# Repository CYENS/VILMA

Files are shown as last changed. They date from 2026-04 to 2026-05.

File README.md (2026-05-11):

# VILMA

This repository contains the codebase for the VILMA (VIsion Language MAnipulation) project, created by the CAIR (Cognitive Artificial Intelligence and Robotics) research group at the CYENS Centre of Excellence. This work was supported by the euROBIN project under the 3rd Open Call for Technology Exchange Programme (Project: "VILMA - Advancing Robotic Manipulation: A Handheld Gripper and Vision-Language Dataset"). 

The repository provides the hardware documentation and software framework for multimodal manipulation data collection using a head-mounted camera, a microphone, and two handheld grippers equipped with cameras and motion tracking systems. It includes tools for sensor synchronization, data acquisition, processing pipelines, and dataset generation.

The VILMA Dataset can be downloaded from our EuroCore Zenodo repository here: https://doi.org/10.5281/zenodo.19708163

## 1. Hardware

Full hardware documentation is available in the `hardware/` folder, that includes:

- Hardware guide
- Full CAD models (STEP, STL, and editable source references)
- Bill of Materials (BOM)
- 3D printing guidelines 
- Assembly instructions with deployment setup guidance
- Interchangeable hard and soft finger configurations
- Integrated HTC VIVE tracker mounting for motion tracking
- GoPro mounting support for egocentric recording
- AprilTags

The design preserves the original UMI pistol-style interaction while introducing project-specific modifications for improved tracking integration, deployment readiness, and real-world data collection reliability.

## 2. Software setup

### 2.1. Clone the repository

```bash
git clone https://github.com/ctheoc/VILMA.git
cd VILMA
```

### 2.2. Create a virtual environment

```bash
python -m venv venv
```

### 2.3. Activate the virtual environment

**Linux / macOS**

```bash
source venv/bin/activate
```

**Windows**

```bash
venv\Scripts\activate
```

### 2.4. Install dependencies

#### 2.4.1 ffmpeg

To check if it's installed, run: 
```bash
which ffprobe
ffprobe -version 
```

If not installed, download from https://ffmpeg.org, or run

**Ubuntu/Debian**
```bash
sudo apt updatesudo apt install ffmpeg 
```

**macOS (Homebrew)**: 
```bash
brew install ffmpeg 
```

#### 2.4.2 Python libraries

```bash
pip install -r requirements.txt
```

## 3. Data Collection

Data are collected using VIVE trackers, GoPro cameras, and microphone.

### 3.1. Finger distance calibration

To account for the severe distortion of the GoPro Hero 13 Black’s 'Ultra Wide HyperView' lens, perform a custom finger distance calibration. Map physical measurements to the pixel distances between the centers of the AprilTags on each finger. 

```bash
python data_collection/vilma_fingers_distance_calibration.py
```

### 3.2. Data Collection setup

#### 3.2.1 Tracking
VIVE trackers and base stations should be connected via SteamVR.
Prerequisites: Download and install SteamVR.
Connect base stations and trackers:
1. Connect the base stations to power.
2. Connect the trackers to the PC:
   - Connect one end of the USB Type-C cable to the dongle cradle, and then plug the dongle into the cradle.
   - Connect the other end of the USB Type-C cable to a USB port on your computer.
   - Note: Keep the dongle at least 45 cm away from the computer and place it where it won’t be moved.
   - From your computer, open the SteamVR app.
   - Click **Menu > Devices > Pair Controller**.
   - Press the Power button for around 2 seconds. The status light will blink blue.
   - Wait for the status light to turn green. This means pairing is successful.
   - In the Controller Pairing window, click **Done**.

#### 3.2.2 Video recording
We use two GoPro HERO13 cameras, each one mounted on each handheld gripper, and a head-mounted GoPro HERO9 camera. HERO13 cameras can be manipulated via this script, while HERO9 is manipulated manually, or via a mobile phone.
Prerequisites: Download GoPro Quik app on the mobile phone.
Setup and connect cameras:
1. Camera settings:
   - GoPro HERO13: 16:9 | 4K | 60 | UHV
   - GoPro HERO9: 4K | 60 | L
2. Connect GoPro HERO13 to the PC:
   - Turn on the cameras and reset wireless connections: **Preferences > Wireless Connections > Reset Connections > Reset All**.
   - Turn on the PC's Bluetooth and Wi-Fi, and delete GoPro cameras from the computers previous connected Bluetooth devices, if any.
   - Select **Pair Device** on cameras.
      
3. Connect GoPro HERO9 to a mobile phone:
   - Turn on the phone's Bluetooth and Wi-Fi, open GoPro Quik, and select GoPro tab.
   - Turn on the camera and select **Connections > Connect Device > Quick App** to connect.

#### 3.2.3 Audio recording
Set up RODE microphone:
1. Connect RX (Receiver) to the PC via USB.
2. Connect TX (Transmitter) to the RX.
3. Select **Wireless GO GX** as the input device in the PC settings.

#### 3.2.4 Check PC audio
Ensure the PC volume is **not muted** so you can hear the 'beep' sound when a recording starts. This sound will be later used to synchronize tracking and video recordings.

### 3.3. Run the data collection script

```bash
python data_collection/vilma_collect_data.py
```

This script creates in the repository root: 
 - a folder with the recorded data named **recordings**, and 
 - a JSON file named **sessions.json** that includes the paths to the data files.

For tracking we use 
https://github.com/TriadSemi/triad_openvr 
at commit d389aacf2a4caa392398613a9daddba15ee24f92.

## 4. Data Processing

### 4.1. Data Processing setup

Make sure that videos exists in the **recordings** folder.
 - Videos captured by the camera mounted on the left gripper under **recordings/left**
 - Videos captured by the camera mounted on the right gripper under **recordings/right**
 - Videos captured by the head-mounted camera under **recordings/head**

To associate these videos with the rest of the recorded data, run:

```bash
python data_processing/vilma_associate_videos.py --json sessions.json --left recordings/left --right recordings/right --head recordings/head
```

Also, an OpeanAI API key is required. 
Create a `.env` file in the repository root with your OpenAI API key:

```bash
echo 'openai_api_key=YOUR_OPENAI_API_KEY' > .env
```

### 4.2. Run the data processing script

The script prepares data before saving into the final dataset:
- Transcribes the recorded instruction (speech-to-text) using OpenAI
- Synchronizes tracking and videos by trimming the videos
- Optimizes videos (H264 codec, and removes audio)
- Computes the distance between the fingers of each gripper by detecting the AprilTags

```bash
python data_processing/vilma_process_data.py --json sessions.json --recordings recordings
```

### 4.3. Extract depth maps

To extract depth maps from the videos using Depth-Anything-V2, run:

```bash
python data_processing/Depth-Anything-V2/run_video.py --encoder vits --sessions-path sessions.json --pred-only --grayscale
```

For depth extraction, we use 
https://github.com/DepthAnything/Depth-Anything-V2 
at commit a561b849ebae10a6f5ef49e26c83cbbcd36c71bf. 
We modified run_video.py for VILMA's purposes.

### 4.4. Video compression

To convert videos (including depth maps) to 720p at 30FPS, run:

```bash
python data_processing/vilma_compress_videos.py --input-dir recordings
```

## 5. Dataset creation

### 5.1. Calculate statistics

Generate task, participants, and locations statistics, and export `tasks_info` from the json file:

```bash
python dataset_creation/vilma_calculate_statistics.py sessions.json --tasks-info-output vilma_tasks_info.json
```

### 5.2 Create the dataset

Create/append the HDF5 structure from the json file:

```bash
python dataset_creation/vilma_create_hdf5_dataset.py --json sessions.json --tasks-info vilma_tasks_info.json --recordings-root recordings --output vilma_dataset.h5
```

Organize video files according to the HDF5 hierarchy:

```bash
python dataset_creation/vilma_organize_videos_by_hdf5.py --h5 vilma_dataset.h5 --recordings-root recordings --output-root /path/to/dataset_root
```

In case you want to blur faces that may appear in the recorded videos, run the following command, which uses *insightface*:

```bash
python dataset_creation/vilma_blur_faces.py
```

### 5.3 Navigate the dataset

Print HDF5 contents (for array datasets, prints only shape and first element or line):

```bash
python dataset_creation/vilma_print_hdf5_contents.py --h5 vilma_dataset.h5
```

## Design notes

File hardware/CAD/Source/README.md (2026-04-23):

# Source CAD Links

This folder contains references to the original editable CAD models used for the VILMA hardware design.

## Full Assembly

- **VILMA Gripper Assembly**  
  https://cad.onshape.com/documents/d9cc1d7e208f3b17cdf52c72/w/7a7459d137796996d25d8c36/e/3712b0b6b9b9e568454d5b5a

## Main Gripper Structure

- **Bottom Plate**  
  https://cad.onshape.com/documents/15c09960880491ea93a360c3

- **Cube**  
  https://cad.onshape.com/documents/9a9afbe52a0a292fa8bf2908

- **Grip**  
  https://cad.onshape.com/documents/39a675e9952b9674d5f9e9bd

- **Handle**  
  https://cad.onshape.com/documents/da0211c3a1cee51d220c0298

- **Top Cover**  
  https://cad.onshape.com/documents/b42c8916bb2e476fafe6626f

## Finger Holders

- **Finger Holder Left**  
  https://cad.onshape.com/documents/33cd6a9c879b5874e04145bc

- **Finger Holder Right**  
  https://cad.onshape.com/documents/0807e3551862e63bd41ff424

## Motion Transmission Parts

- **Gear Left**  
  https://cad.onshape.com/documents/71062ec68bcd396d6c51dda4

- **Gear Right**  
  https://cad.onshape.com/documents/da0211c3a1cee51d220c0298

- **Linkage Left**  
  https://cad.onshape.com/documents/a32be336220d6b551629de31

- **Linkage Right**  
  https://cad.onshape.com/documents/39a675e9952b9674d5f9e9bd

## Interchangeable Fingers

- **Hard Finger 1**  
  https://cad.onshape.com/documents/687b9313af9450aa09ee8f99

- **Hard Finger 2**  
  https://cad.onshape.com/documents/56f98ccaed0c1dc6005e7eaa

- **Soft Gripper Finger 1**  
  https://cad.onshape.com/documents/5d6f420d0f53ab1009077a6b

- **Soft Gripper Finger 2**  
  https://cad.onshape.com/documents/5d6f420d0f53ab1009077a6b

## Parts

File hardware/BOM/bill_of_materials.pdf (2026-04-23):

## Bill of Materials

A. Main Gripper Body
Part | Quantity | Link | Price (per unit)
eSUN PLA PRO Warm White 1kg | 0.5 | Link (https://amazon.de/eSUN-PLA-Filament-Dimensional-Lite/dp/B0BT9F3BCD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) | €10.73
MGN9C 150 mm Linear Rail | 2 | Link (https://www.amazon.de/CNCMANS-Miniature-Bearing-Engraving-Machine/dp/B0BPRZRBZV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) | €9.99
M3 Screws and Nuts set | See notes | Link (https://www.amazon.de/-/en/WZHUIDA-Cylinder-Hexagon-Assortment-Machines/dp/B0DHC27MQP) Link (https://www.amazon.de/-/en/sourcingmap%C2%AE-Thread-Socket-Screws-Bolts/dp/B01DIUJO14) | €8.49 €8.19
Compression Spring, 10 mm OD, 0.7 mm wire size, 50 mm free length | 1 | Link (https://www.amazon.de/dp/B092HL27R7?s=industrial&aref=OsMq71KuMa&sp_csd=d2lkZ2V0TmFtZT1zcF9kZXRhaWw) | €8.49
M5 Nut | 1 | Link (https://www.amazon.de/-/en/M5-Stainless-DIN439-Washers-Threaded/dp/B0DCNM6BGY) | €6.49
Super Lube 21030 | 1 | Link (https://www.amazon.de/-/en/Super-Lube-21030-Synthetic-Grease/dp/B000XBH9HI) | €19.90
Double-sided Tape | 1 | Link (https://www.amazon.de/Emitever-Double-sided-68211-furniture-high-performance/dp/B0DSK8F25P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) | €15.99
Printed ArUco Tags (US Letter) | 1 set | Link (https://drive.google.com/drive/folders/1pCiuABTyev7k4EWJ3LQ-zKz3ZHjzeIDF?usp=sharing) | -
1/4-inch Bolt and Nut | 1 | Link (https://www.amazon.de/-/en/Stainless-Pieces-4-20UNC-Screws-Assortment/dp/B0CKCKLPQM?s=industrial) | €18.09

Notes

M3 Screws and Nuts set includes:

- 14 × M3 × 8 mm
- 2 × M3 × 12 mm
- 4 × M3 × 25 mm
- 6 × M3 × 35 mm
B. Gripper Fingers

Part | Quantity | Link | Price (per unit)
Polymaker TPU 95A Orange 750 g | 0.25 | Link (https://www.amazon.de/-/en/Polymaker-PolyFlex-TPU-95A-Orange/dp/B09KKZLZVR) | €34.95
3M TB641 / GM641 Grip Tape, 25mm wide, 5 m | 0.05 | Link (https://www.amazon.de/-/en/Qzakce-Non-Slip-Self-Adhesive-Waterproof-Touching/dp/B0GH7H5W78?s=industrial) | €8.99
C. Camera and Recording Components
Part | Quantity | Link | Price (per unit)
GoPro Hero 13 | 1 | Link (https://www.amazon.de/-/en/GoPro-HERO13-Black-Waterproof-Compatibility/dp/B0DCQVQDQ7) | €265.44
Micro SD Card (V30 rated) | 1 | Link (https://www.amazon.de/-/en/SanDisk-microSDXC-RescuePRO-Smartphones-Transfer/dp/B09X7DMBVF) | €44.99
HTC VIVE Tracker 3.0 | 1 | Link (https://www.vive.com/eu/accessory/tracker3/) | €154.00

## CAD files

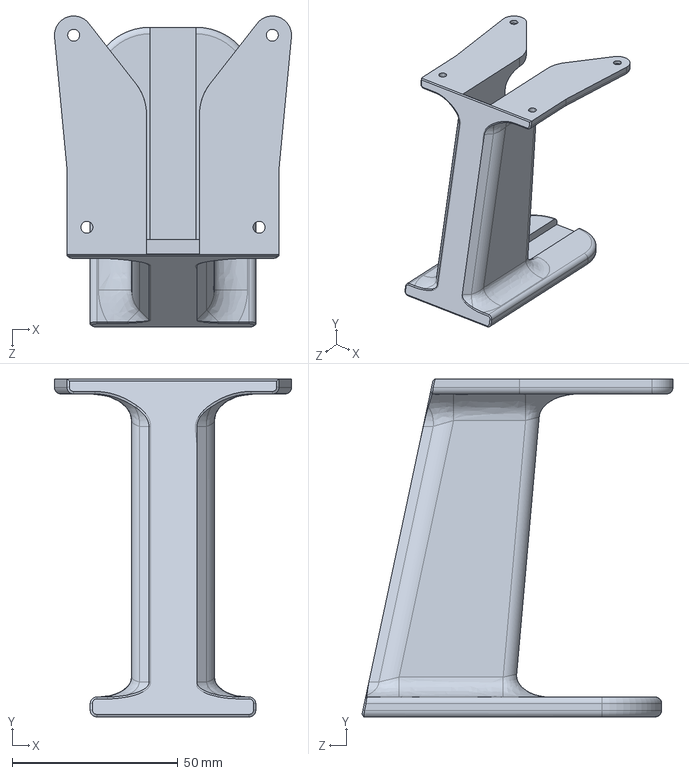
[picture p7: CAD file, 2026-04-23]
hardware/CAD/STEP/gripper - grip.STEP
71.6 x 102.0 x 93.9 mm

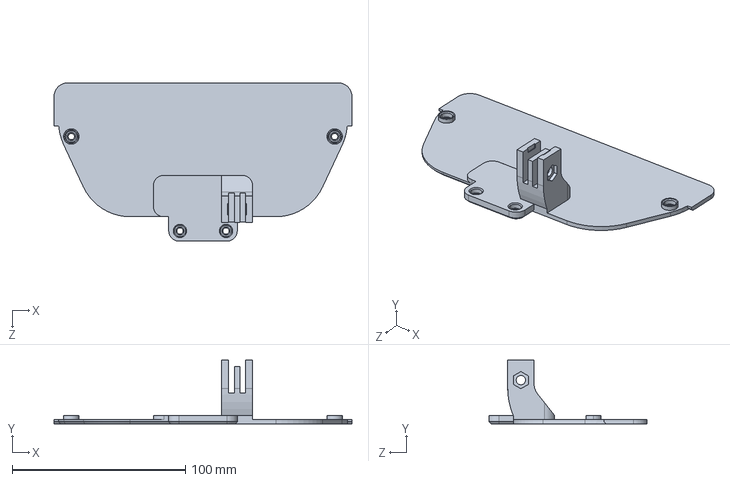
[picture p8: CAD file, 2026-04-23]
hardware/CAD/STEP/gripper - top_cover 2026.STEP
172.0 x 36.7 x 91.4 mm

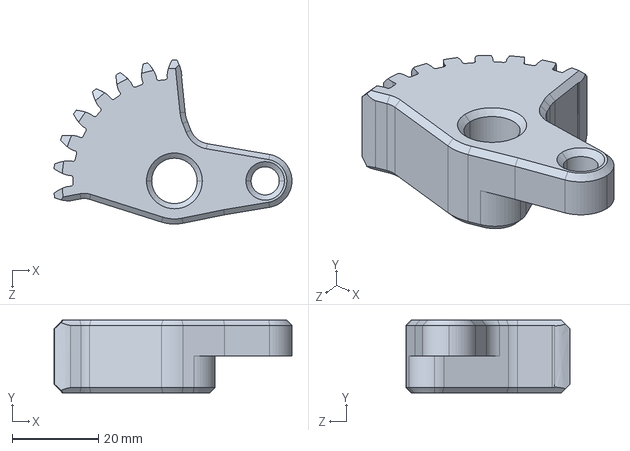
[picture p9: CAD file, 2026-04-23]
hardware/CAD/STEP/gripper - gear_left.STEP
55.1 x 16.8 x 38.0 mm

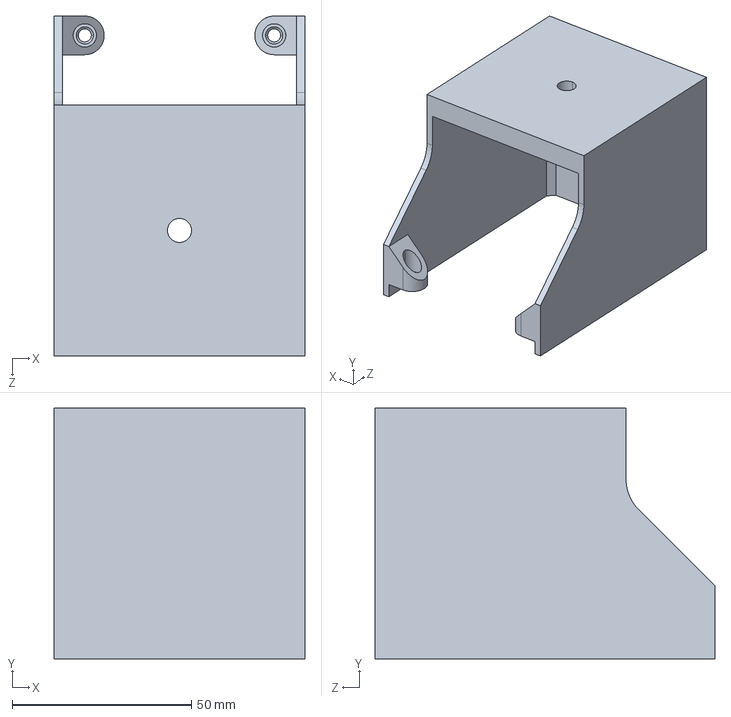
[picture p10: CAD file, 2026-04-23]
hardware/CAD/STEP/gripper - cube.STEP
70.0 x 70.0 x 94.8 mm

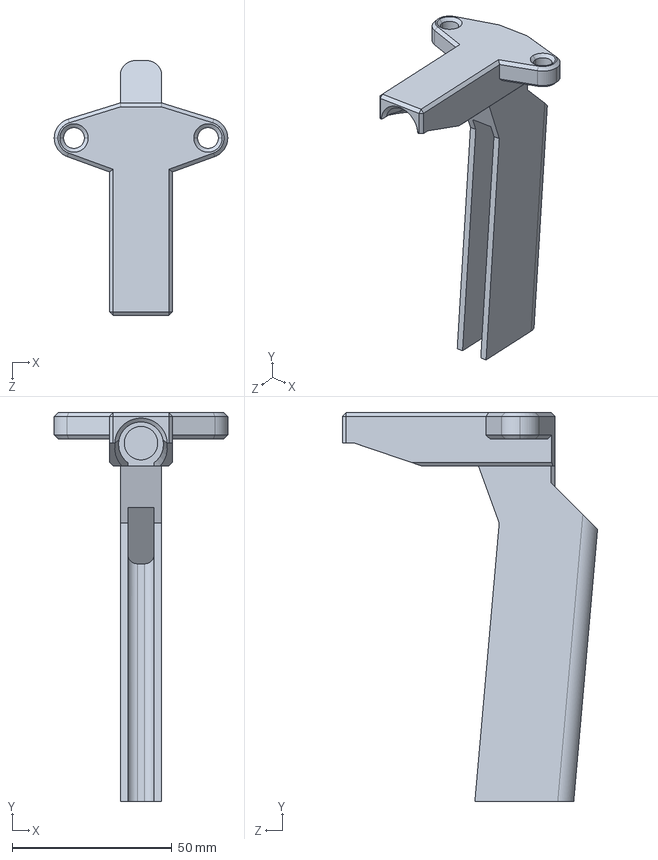
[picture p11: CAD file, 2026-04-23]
hardware/CAD/STEP/gripper - handle.STEP
54.4 x 121.9 x 80.0 mm

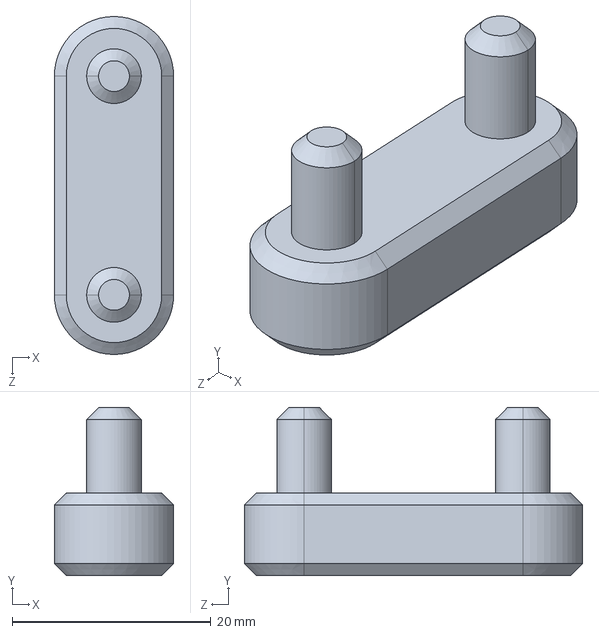
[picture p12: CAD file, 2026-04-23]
hardware/CAD/STEP/gripper - linkage_left.STEP
12.0 x 16.9 x 34.0 mm

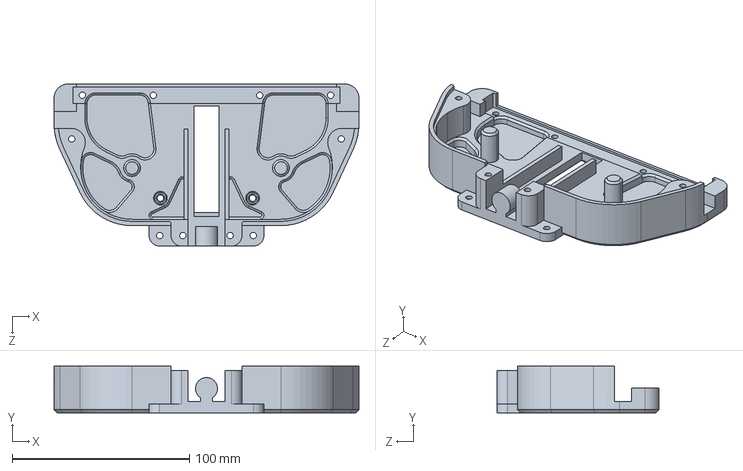
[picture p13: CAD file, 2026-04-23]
hardware/CAD/STEP/gripper - bottom_plate.STEP
172.0 x 26.3 x 91.4 mm

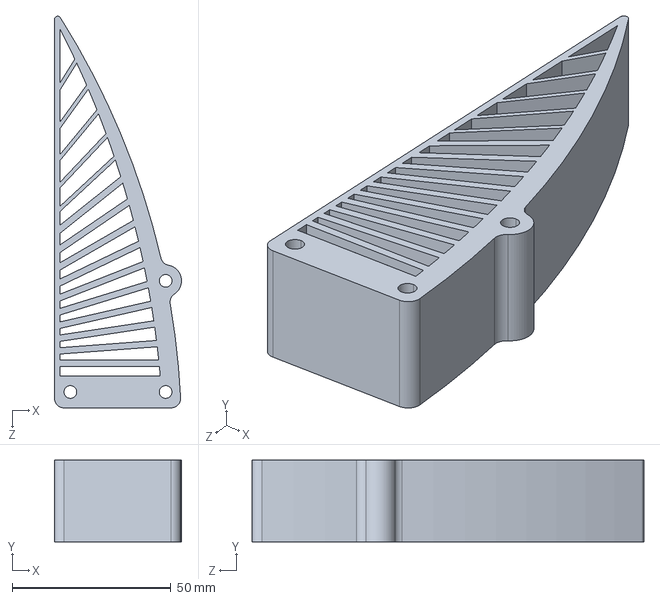
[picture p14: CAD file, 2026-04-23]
hardware/CAD/STEP/soft_gripper_finger.STEP
40.0 x 25.8 x 123.4 mm

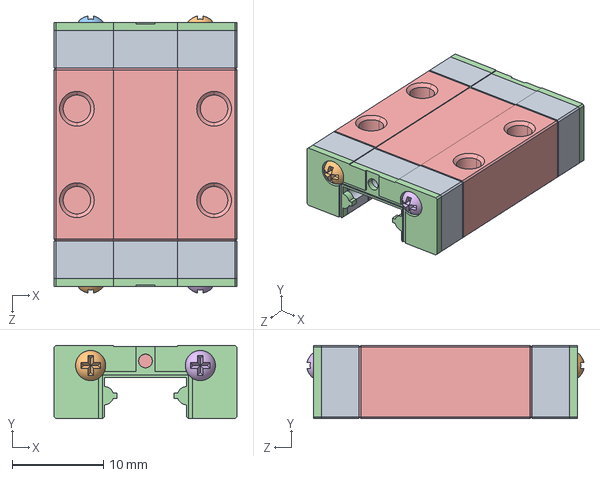
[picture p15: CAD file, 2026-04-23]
hardware/CAD/STEP/v1_MGN9-H_По умолчанию.STEP
20.0 x 8.00 x 30.3 mm

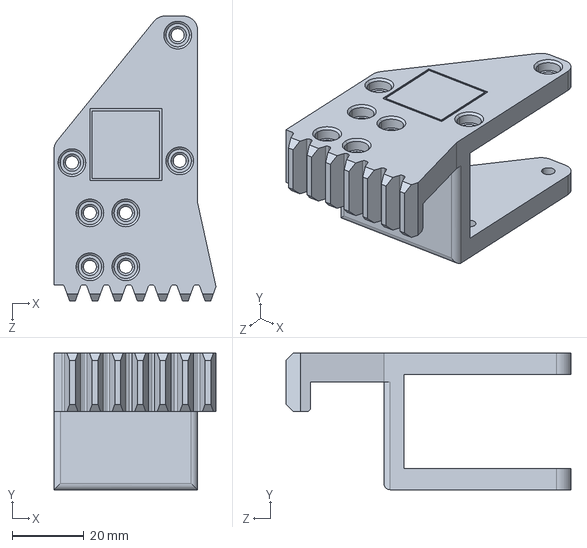
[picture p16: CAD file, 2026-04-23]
hardware/CAD/STEP/gripper - finger_holder_right.STEP
45.1 x 38.0 x 79.3 mm

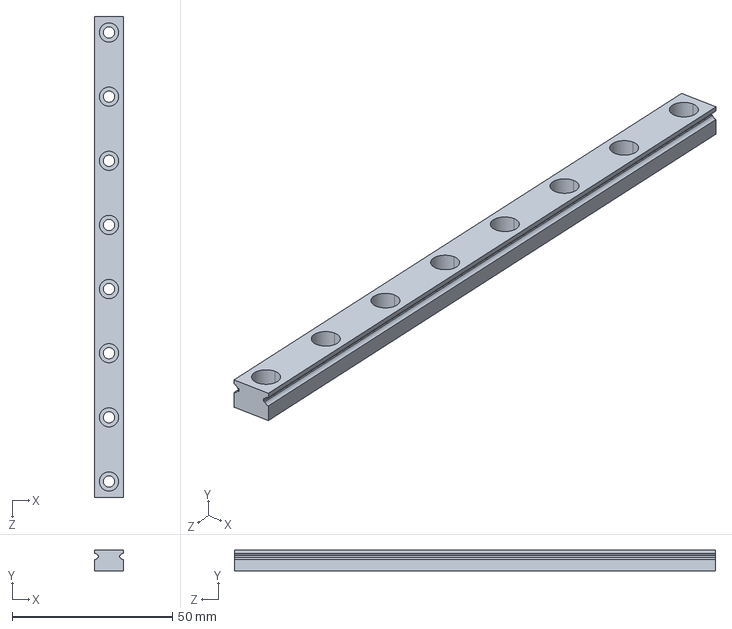
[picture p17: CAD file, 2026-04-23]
hardware/CAD/STEP/v1_MGN9_250_По умолчанию.STEP
9.00 x 6.50 x 150.0 mm

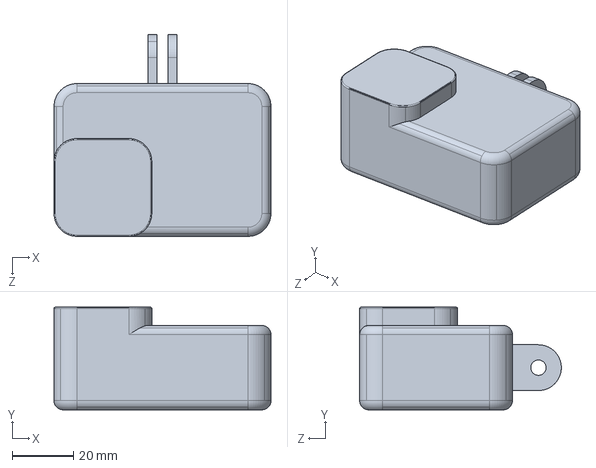
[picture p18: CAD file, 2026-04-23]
hardware/CAD/STEP/GoPro9.STEP
71.0 x 33.6 x 66.0 mm

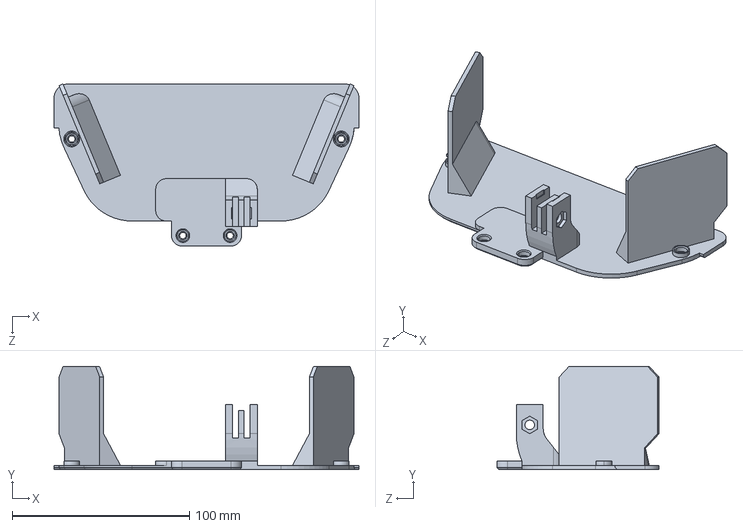
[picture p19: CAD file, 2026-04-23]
hardware/CAD/STEP/gripper - top_cover.STEP
172.0 x 58.2 x 91.4 mm

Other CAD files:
hardware/CAD/STEP/gripper - gear_right.STEP
hardware/CAD/STEP/MGN9_По умолчанию.STEP
hardware/CAD/STEP/gripper - linkage_right.STEP
hardware/CAD/STEP/VILMA Handheld Device.STEP
hardware/CAD/STEP/gripper - finger_holder_left.STEP

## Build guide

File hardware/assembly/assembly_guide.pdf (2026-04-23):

VILMA

Hardware Building Guide

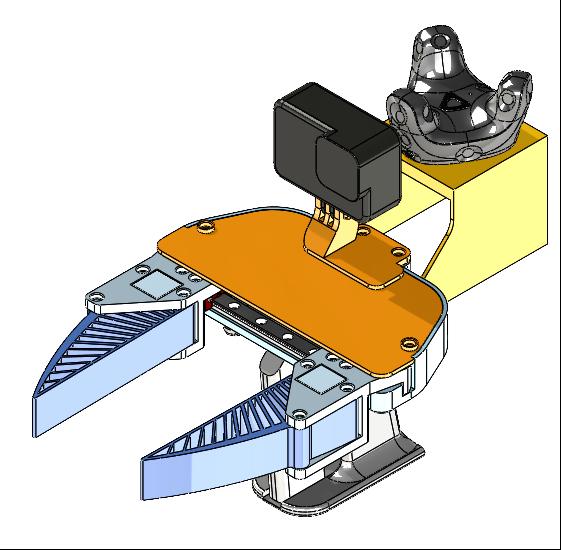
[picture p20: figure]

Assembly Instructions

The following steps describe the assembly process of the modified UMI handheld gripper.

### 1. Gather all required components

Collect all printed parts, mechanical components, and tools before starting the assembly.

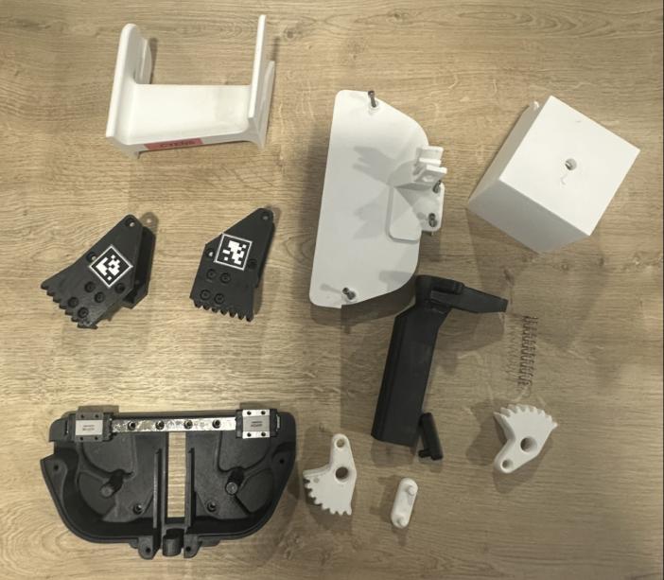
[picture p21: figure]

### 2. Install the linear rail on the base plate

Secure the linear rail onto the bottom plate using the appropriate fasteners and lubricate.

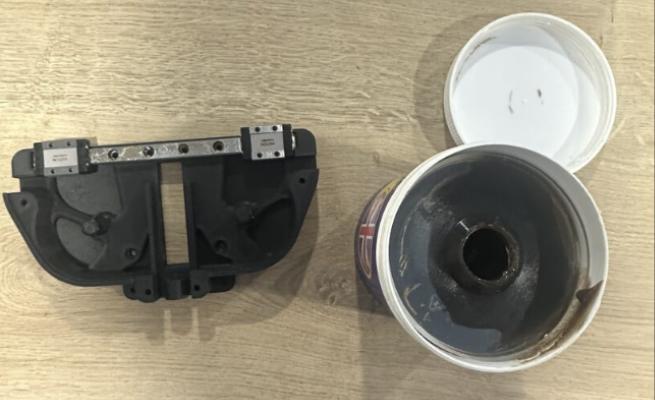
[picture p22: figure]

### 3. Install the hand grip

Lubricate and attach the grip component to the main structure.

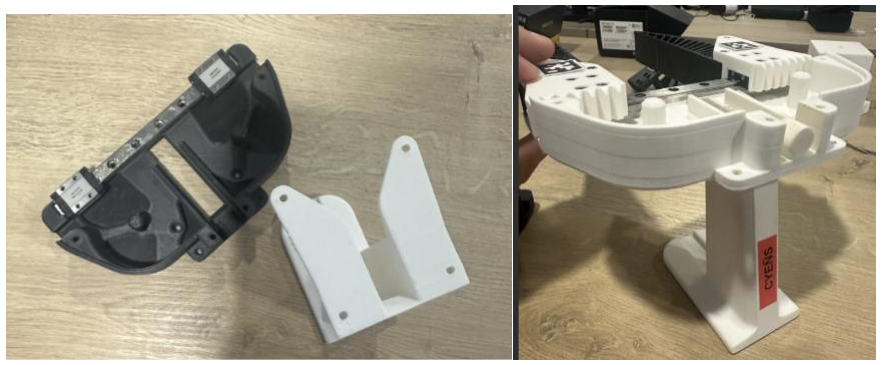
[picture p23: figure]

### 4. Install finger holders

Mount the left and right finger holders in their designated positions.

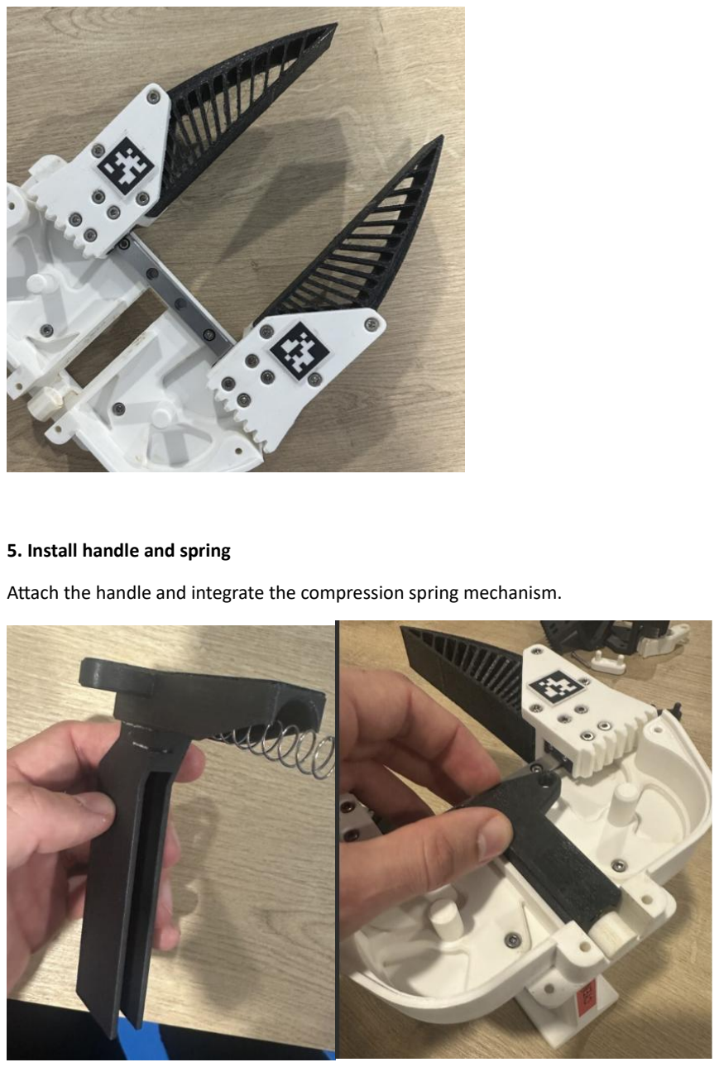
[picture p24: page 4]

### 5. Install handle and spring

Attach the handle and integrate the compression spring mechanism.

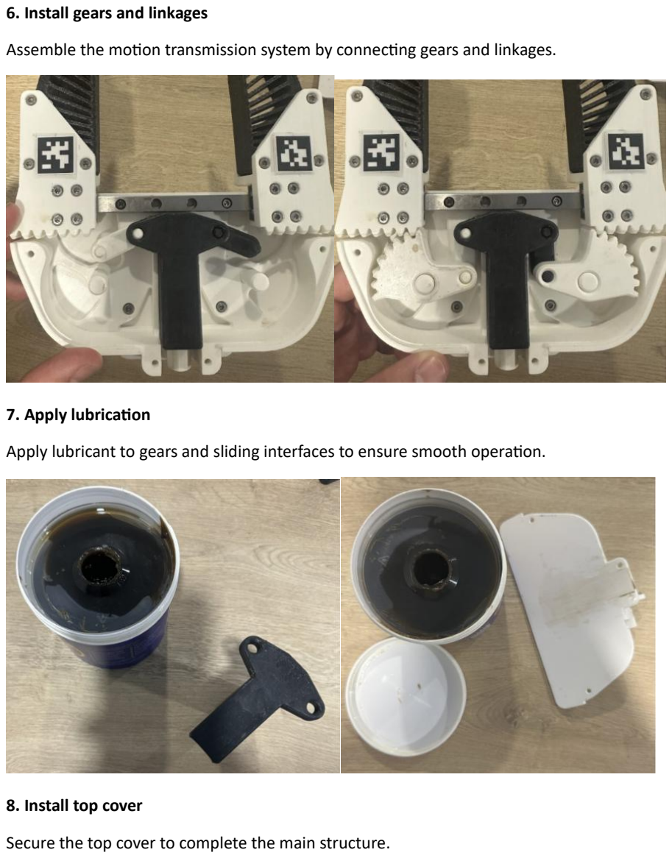
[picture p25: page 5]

### 6. Install gears and linkages

Assemble the motion transmission system by connecting gears and linkages.

### 7. Apply lubrication

Apply lubricant to gears and sliding interfaces to ensure smooth operation.

### 8. Install top cover

Secure the top cover to complete the main structure.

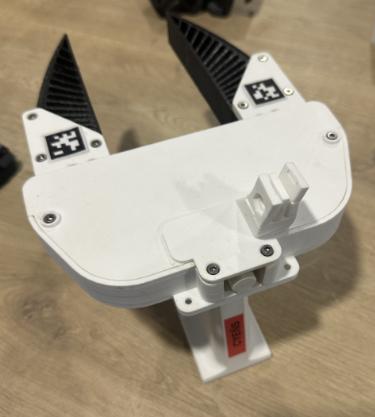
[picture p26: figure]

### 9. Install balancing cube

Attach the cube component to improve balance and stability.

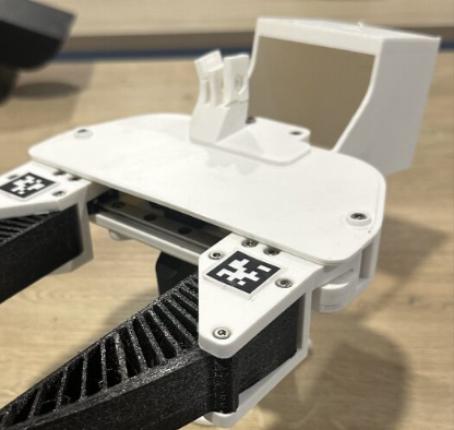
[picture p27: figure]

### 10. Apply grip tape

Place grip tape on the appropriate contact surfaces for improved handling.

### 11. Install fingers

Attach either the soft TPU fingers or the hard PLA fingers depending on the use case.

### 12. Perform final adjustments

Check alignment, tighten all fasteners, and verify smooth motion.

### 13. Apply tracking markers

Attach the printed ArUco markers to the designated locations.

### 14. Mount VIVE tracker

Install the VIVE tracker using the 1/4-inch mounting interface.

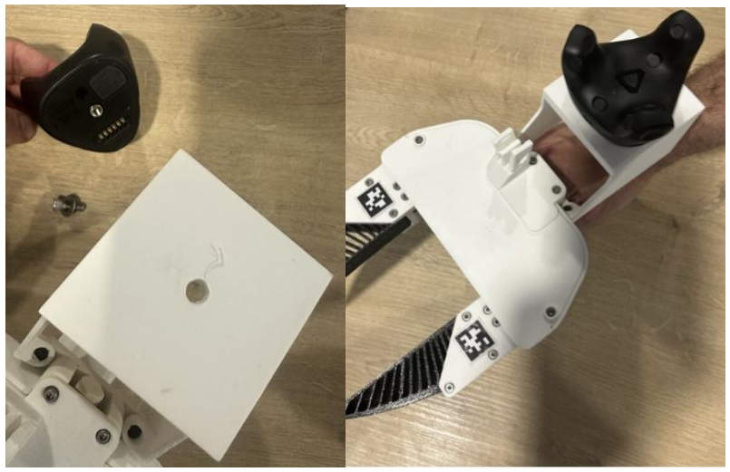
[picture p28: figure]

### 15. Mount GoPro camera

Attach the GoPro camera for egocentric recording.

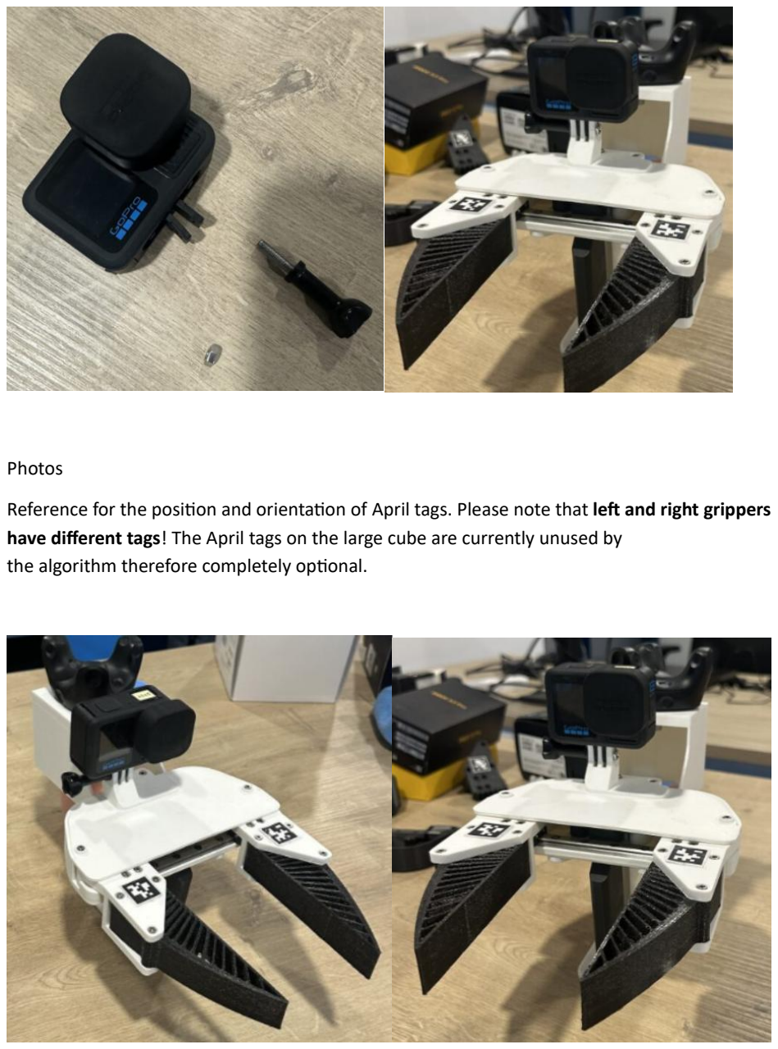
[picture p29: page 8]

Photos

Reference for the position and orientation of April tags. Please note that left and right grippers have different tags! The April tags on the large cube are currently unused by
the algorithm therefore completely optional.

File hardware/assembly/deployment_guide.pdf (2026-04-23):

## Deployment Hardware Guide for Data Collection

Bill of Materials

Part | Quantity | Link | Price (per unit)
Modified UMI handheld device | 2 | - | €624.72
HTC VIVE Base Station | 2 | Link (https://www.vive.com/eu/accessory/base-station2/) | €245.00
Tripod | 2 | Link (https://www.amazon.de/Selens-Kit-Photography-Adjustable-Accessories/dp/B07RHT8T2C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) | €39.99
GoPro Hero 9 (head-mounted & accessories) | 1 | Link (https://www.amazon.de/-/en/GoPro-SPBL1-Hero9-black/dp/B08G2HBBB6) Link (https://www.amazon.de/oGoDeal-Waterproof-Protective-Snorkelling-Accessories/dp/B09YYGKQYZ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) | €179.99 €49.99
Mobile phone for GoPro monitoring/pairing | 1 | -
Laptop / workstation | 1 | -
Microphone Rode Gen 3 | 1 | Link (https://www.amazon.de/-/en/Wireless-2-Channel-Microphone-Interview-Protection-R%C3%98DE-GO-III-Set-WSBK/dp/B0DQ1YY8KG) | €235.90
Chargers and charging cables | as needed | -
Extension cables | as needed | -
Power adapters | as needed | -
Spare parts for modified UMI | as needed | -
Spare soft fingers / hard fingers | as needed | -

Setup Instruction

1. Prepare the workspace.
2. Position the two VIVE base stations.
3. Assign different base-station channels.
4. Launch SteamVR with the required null-driver configuration.
5. Synchronize the workstation time.
6. Power on and pair the VIVE trackers.
7. Mount the trackers on the modified UMI devices.

8. Perform room and tracker calibration using the 17 cm tracker offset reference.
9. Power on and pair the mounted GoPro Hero 13 cameras.
10. Prepare the optional head-mounted GoPro Hero 9.
11. Prepare the microphone.
12. Launch vilma_data_collection.py.
13. Select unimanual/bimanual mode and optional head-mounted camera mode.
14. Confirm all device connections.
15. Start recording.
16. Execute the task.
17. Stop recording and save the run.
18. Record metadata and inspect tracker outliers.
19. Inspect the handheld hardware and replace parts if needed.
20. Reset the setup for the next run.

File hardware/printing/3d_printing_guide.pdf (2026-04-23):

## 3D printing Instructions

Checkout our CURA 3mf examples for more detailed parameters:

https://drive.google.com/drive/folders/15vFeCd-fEt-NOYkRXebhpDGm5D2zX3MM?usp=sharing (https://drive.google.com/drive/folders/15vFeCd-fEt-NOYkRXebhpDGm5D2zX3MM?usp=sharing)

3D Printed Parts List

Part Name | Quantity | Material | Category | Notes
Bottom Plate | 1 | PLA+ | Main Structure | Main lower structural plate
Cube | 1 | PLA+ | Main Structure | Central structural block
Finger Holder Left | 1 | PLA+ | Finger Holder | Left finger support
Finger Holder Right | 1 | PLA+ | Finger Holder | Right finger support
Gear Left | 1 | PLA+ | Motion Transmission | Left actuation gear
Gear Right | 1 | PLA+ | Motion Transmission | Right actuation gear
Grip | 1 | PLA+ | Main Structure | Main hand-contact body
Handle | 1 | PLA+ | Main Structure | Handle body
Linkage Left | 1 | PLA+ | Motion Transmission | Left linkage element
Linkage Right | 1 | PLA+ | Motion Transmission | Right linkage element
Top Cover 2026 | 1 | PLA+ | Main Structure | Upper cover plate
Hard Finger 1 | 1 | PLA+ | Interchangeable Finger | Left/right hard-finger pair component
Hard Finger 2 | 1 | PLA+ | Interchangeable Finger | Left/right hard-finger pair component
Soft Gripper Finger 1 | 1 | TPU 95A | Interchangeable Finger | Left/right soft-finger pair component
Soft Gripper Finger 2 | 1 | TPU 95A | Interchangeable Finger | Left/right soft-finger pair component

Note

Only one interchangeable finger pair is used in the final assembly at a time:

- either the soft-finger pair,
- or the hard-finger pair.

3D Printing Guidelines

Common Print Parameters for PLA+ Parts

The following settings were used as the common baseline for all PLA+ printed components unless otherwise specified:

- Material: eSun PLA+
- Nozzle diameter: 0.6 mm
- Layer height: 0.3 mm
- Wall thickness: 1.2 mm
- Top-bottom thickness: 1.2 mm
- Infill: 20% Gyroid
- Printing temperature: 190°C
- Cooling fan: 100%

Finger Print Parameters for TPU Parts

The following settings were used for the flexible finger components:

- Material: Polymaker TPU 95A
- Nozzle diameter: 0.6 mm
- Layer height: 0.3 mm
- Infill: 100% Lines
- Printing temperature: 255°C
- Cooling fan: 0%

Part-Specific Printing Table

Print Group | Part | Material | Infill % | Support Required | Wall Thickness (mm) | Top-Bottom Thickness (mm) | Notes
Print 1: Gripper Covers | Bottom Plate | PLA+ | 20 | No | 1.2 | 1.2 | Use common PLA+ print settings
| Top Cover 2026 | PLA+ | 20 | No | 1.2 | 1.2 | Use common PLA+ print settings
Print 2: Gripper Internals | Grip | PLA+ | 100 | No | 1.8 | 1.2 | Increased infill for higher structural strength
| Handle | PLA+ | 20 | No | 1.2 | 1.2 | Use common PLA+ print settings
| Cube | PLA+ | 20 | No | 1.2 | 1.2 | Use common PLA+ print settings
| Finger Holder Left | PLA+ | 20 | Yes | 1.2 | 1.2 | Print with supports
| Finger Holder Right | PLA+ | 20 | Yes | 1.2 | 1.2 | Print with supports
| Gear Left | PLA+ | 20 | No | 1.2 | 1.2 | Use common PLA+ print settings
| Gear Right | PLA+ | 20 | No | 1.2 | 1.2 | Use common PLA+ print settings

| Linkage Left | PLA+ | 20 | No | 2.4 | 1.8 | Increased wall and top-bottom thickness
| Linkage Right | PLA+ | 20 | No | 2.4 | 1.8 | Increased wall and top-bottom thickness
Print 3: Gripper Fingers | Hard Finger 1 | PLA+ | 100 | No | 1.2 | 1.2 | Rigid finger configuration
| Hard Finger 2 | PLA+ | 100 | No | 1.2 | 1.2 | Rigid finger configuration
| Soft Gripper Finger 1 | TPU 95A | 100 | No | — | — | Print with TPU finger settings
| Soft Gripper Finger 2 | TPU 95A | 100 | No | — | — | Print with TPU finger settings

3D Printing Guidelines

The following guidelines summarize the recommended workflow for fabricating the modified UMI components.

1. Select a reliable FDM 3D printer capable of printing PLA+ and TPU materials.
2. Install a 0.6 mm nozzle to reduce print time and improve structural robustness.
3. Level the print bed carefully to ensure proper first-layer adhesion.
4. Import the provided .3mf or .stl files into the slicer software (e.g., Cura).
5. Apply part-specific print settings according to the component category (structure, linkage, fingers).
6. Use standard PLA+ settings for all structural components.
7. Use dedicated TPU settings (low cooling, high infill) for soft-finger components.
8. Adjust tolerances in CAD if necessary to ensure proper fit between moving parts.

9. Customize the hand grip geometry in CAD if user-specific ergonomics are required.
10. Prepare the printer by cleaning the build plate and verifying material loading.
11. Start the print and monitor the first layers to confirm correct adhesion.

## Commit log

2026-04-23 Move AprilTags pdf in hardware/printing
2026-04-24 Update camera connection instructions in README
